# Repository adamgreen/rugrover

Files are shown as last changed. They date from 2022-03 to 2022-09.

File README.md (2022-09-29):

# Rug Rover
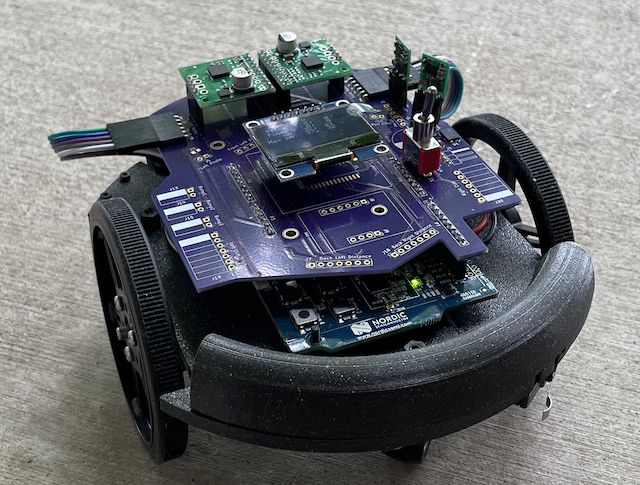
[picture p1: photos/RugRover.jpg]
RugRover Photo of Work In Progress


## **Project on Hold**
I am putting this project on hold for a few months while I switch back to my [Robomagellan robot project](https://github.com/adamgreen/Ferdinand20/#readme) in hopes of the SRS Robothon competition being run in 2023. I will take lessons learned this year while working on my RugRover and apply them to my Robomagellan bot, Ferdinand20.

## Project Overview
My copy of Mobile Robotics

When I first started pursuing robotics as a hobby back in the late 1990s, one of the first books I read was ["Mobile Robots: Inspiration to Implementation" by Joseph L. Jones and Anita M. Flynn](https://www.amazon.com/Mobile-Robots-Inspiration-Implementation-Second/dp/B0087P7X2S). I just read it again recently and the core lessons covered by the book are just as useful today as they were back at that time even though some of the technology discussed is now a bit out of date. The mechanical, electrical, motor physics, and behavior based programming topics covered are all still relevant. The Motorola 68HC11 microcontroller and Interactive C programming language are examples of some of the more dated topics.

After reading the book for the first time, I ordered one of the [Rug Warrior Pro kits](http://www.robotbooks.com/rug_warrior.htm) and assembled it. I enjoyed putting it together but never did a lot of experimentation with it as I never really got one of the wheel encoders to work properly. It seemed to pick up noise from the motor as erroneous encoder tick counts.

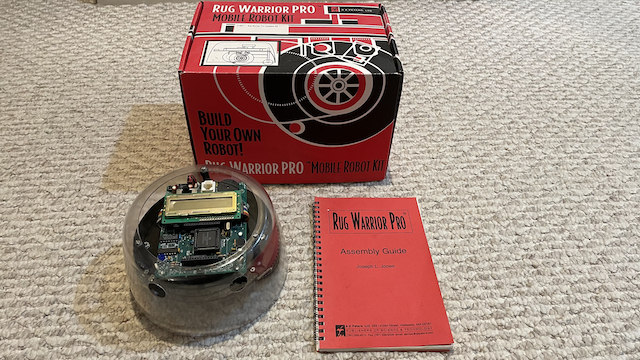
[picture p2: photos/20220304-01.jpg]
My original Rug Warrior Pro


Having recently reread the book, I thought it would be fun to build a comparable robot using more recent technology. This Rug Rover project is my attempt to build such a robot. It features will include:
* Similar sensors/actuators:
  * Motors with encoders
  * IR proximity sensors
  * Bumper switches
  * Microphone
  * Speaker
  * Pyroelectric sensor
  * Photo Cell light level detectors
  * LCD
* Add in IR based downward facing cliff detectors so that I can run the robot in my loft and hopefully write software that stops it from trying to make a run down the stairs.
* More modern nRF52 BLE capable microcontroller:
  * Exploit the BLE capabilities of this microcontroller to enable wireless debugging and programming.
  * Program in C/C++ using GCC.
  * Debug code using GDB.
* Mechanical components will be designed in CAD and 3D printed.
* Use KiCAD to design a custom PCB for this bot. The first iteration of the PCB will be a shield for a nRF52 development kit that I already own. Later I can design a new PCB that uses a small nRF52 module, like those [offered by Adafruit](https://www.adafruit.com/product/4077).

## Reading List
In addition to reading ["Mobile Robots: Inspiration to Implementation" by Joseph L. Jones and Anita M. Flynn](https://www.amazon.com/Mobile-Robots-Inspiration-Implementation-Second/dp/B0087P7X2S) I have also read a few other books to learn more about robot design, building, and programming while working on this project:

<a href="https://www.amazon.com/Navigating-Mobile-Robots-Systems-Techniques/dp/156881058X">Navigating Mobile Robots: Systems and Techniques</a>
<a href="https://www.amazon.com/Kalman-Filter-Beginners-MATLAB-Examples/dp/1463648359">Kalman Filter for Beginners with MATLAB Examples</a>

**Note:** A free PDF version of the **Navigating Mobile Robots book by Borenstein et al** shown above is also available [here](http://www-personal.umich.edu/~johannb/Papers/pos96rep.pdf).

## Bill of Materials
| Quantity | Part Name / Link |
|---|-|
| 2 | [63:1 Metal Gearmotor 20Dx43L mm 6V CB with Extended Motor Shaft](https://www.pololu.com/product/3714) |
| 1 | [Magnetic Encoder Pair Kit for 20D mm Metal Gearmotors, 20 CPR, 2.7-18V](https://www.pololu.com/product/3499) |
| 2 | [TB9051FTG Single Brushed DC Motor Driver Carrier](https://www.pololu.com/product/2997) |
| 1 | [Pololu Multi-Hub Wheel w/Inserts for 3mm and 4mm Shafts - 80×10mm, Black, 2-Pack](https://www.pololu.com/product/3690) |
| 1 | [Supporting Swivel Caster Wheel - 1.3" Diameter](https://www.adafruit.com/product/2942) |
| 1 | [Pololu 3.3V, 500mA Step-Down Voltage Regulator D24V5F3](https://www.pololu.com/product/2842) |
| 1 | [Pololu 5V, 500mA Step-Down Voltage Regulator D24V5F5](https://www.pololu.com/product/2843) |
| 1 | [Pololu 12V Step-Up Voltage Regulator U3V40F12](https://www.pololu.com/product/4016) |
| 1 | [Adafruit I2S 3W Class D Amplifier Breakout - MAX98357A](https://www.adafruit.com/product/3006) |
| 1 | [Mini Oval Speaker - 8 Ohm 1 Watt](https://www.adafruit.com/product/3923) |
| 1 | [Adafruit PDM MEMS Microphone Breakout](https://www.adafruit.com/product/3492) |
| 1 | [Graphical OLED Display: 128x64, 1.3", White, SPI](https://www.pololu.com/product/3760) |
| 1 | [MCP23018T-E/SO - I/O Expander 16 I²C 3.4 MHz 28-SOIC](https://www.digikey.com/en/products/detail/microchip-technology/MCP23018T-E-SO/2002549) |
| 2 | [VL6180X Time-of-Flight Distance Sensor Carrier with Voltage Regulator, 60cm max](https://www.pololu.com/product/2489) |
| 5 | [VL53L1X Time-of-Flight Distance Sensor Carrier with Voltage Regulator, 400cm Max](https://www.pololu.com/product/3415) |
| 2 | [Photo cell (CdS photoresistor)](https://www.adafruit.com/product/161) |
| 3 | [Snap-Action Switch with 15.6mm Bump Lever: 3-Pin, SPDT, 5A](https://www.pololu.com/product/1405) |
| 1 | [PIR Motion Sensor](https://www.pololu.com/product/2731) |
| 1 | [Adafruit Precision NXP 9-DOF Breakout Board - FXOS8700 + FXAS21002](https://www.adafruit.com/product/3463) |
| 1 | [Diode Schottky 60 V 7A Surface Mount TO-277A ](https://www.digikey.com/en/products/detail/vishay-general-semiconductor-diodes-division/SS10P6-M3-86A/2152231) |
| 1 | [Toggle Switch SPDT Through Hole](https://www.digikey.com/en/products/detail/e-switch/100SP1T1B4M2QE/378824?s=N4IgTCBcDaIKIHEwGYCsqC0A5AIiAugL5A) |
| 1 | [Rechargeable NiMH Battery Pack: 6.0 V, 2200 mAh, 3+2 AA Cells, JR Connector](https://www.pololu.com/product/2224) |
| 2 | [Red Dirt Derby 2 oz Tungsten Putty Weights](https://www.amazon.com/Red-Dirt-Derby-Tungsten-Pinewood/dp/B06Y5FDLL6) |
| 1 | [1/4" OD Black Latex Tubing for Bumper Skirt Standoffs](https://www.amazon.com/LATEX-TUBING-602-BLACK-10FT/dp/B074NCLZSW) |
| 1 | [Nordic Semiconductor nRF52 Development Kit](https://www.digikey.com/en/products/detail/nordic-semiconductor-asa/NRF52-DK/5773879) |
| X | Already owned 0805 passives, 0.1" headers, etc. |
| X | Already owned M2, M2.5, and M3 hardware |

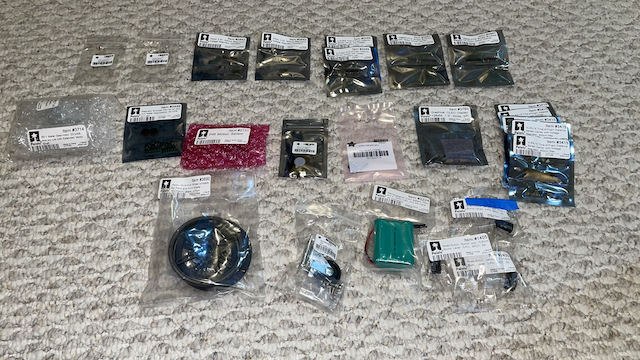
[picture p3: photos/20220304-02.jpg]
Parts


**Notes:** I didn't end up with enough spare pins on version 1 of the PCB to connect the microphone and I2S audio components. I will experiment with these devices off of the robot for now and then add them on the next revision of the board.

## Mechanical Design
When it comes to robot building, the mechanical portions are my weakest area. On some other robot projects I have started with software drivers and then never got around to even starting on the mechanical portions since I wasn't really looking forward to it. Best to get it out of the way first on this project. Doing it first also means that I have something physical to look at and hold earlier in the project to help keep me motivated.

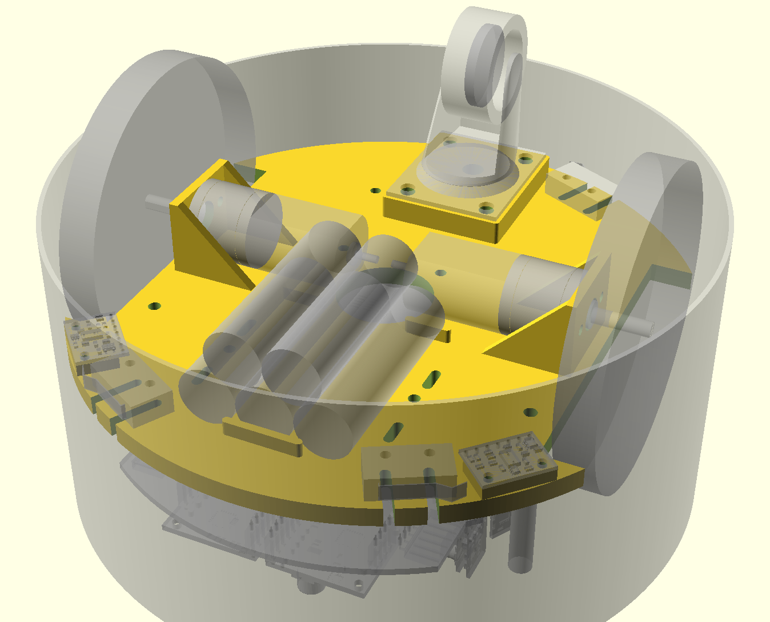
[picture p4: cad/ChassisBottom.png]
Chassis Bottom


**Mechanical Highlights:**
* 3D print the mechanical parts for this robot in PETG.
* Use OpenSCAD for the 3D design.
* The following parts will be mounted to the underside of the robot chassis:
  * 2 x Motors
  * 1 x Caster
  * 2 x Cliff Detection Sensors (VL6180X) mounted in front of the wheels.
  * 3 x Micro Switches to detect bumper collisions.
  * 1 x 5 cell (6V) NiMH rechargeable battery.
* Chassis has holes for attachment of following parts to the topside of the chassis:
  * 5 x Standoffs for Nordic nRF52-DK Development Kit PCB to which shield with remaining sensors/actuators will be mounted.
  * 3 x Flexible Rubber Tube Standoffs to which the bumper skirt is attached, allowing bumper to move and press against micro switches when an obstacle is encountered.
  * A separate curved cylindrical 3D printed holder that goes on the back of the robot to hold ~100g of tungsten counter weight. This moves the center of mass closer to the caster so that the robot doesn't nose dive during quick decelerations. Only having room for the batteries at the front of the bot increased the need for this counterweight.
* A separate bumper skirt is printed to enclose the robot.
  * It is mounted to the chassis on flexible rubber tube standoffs like the Rug Warrior Pro.

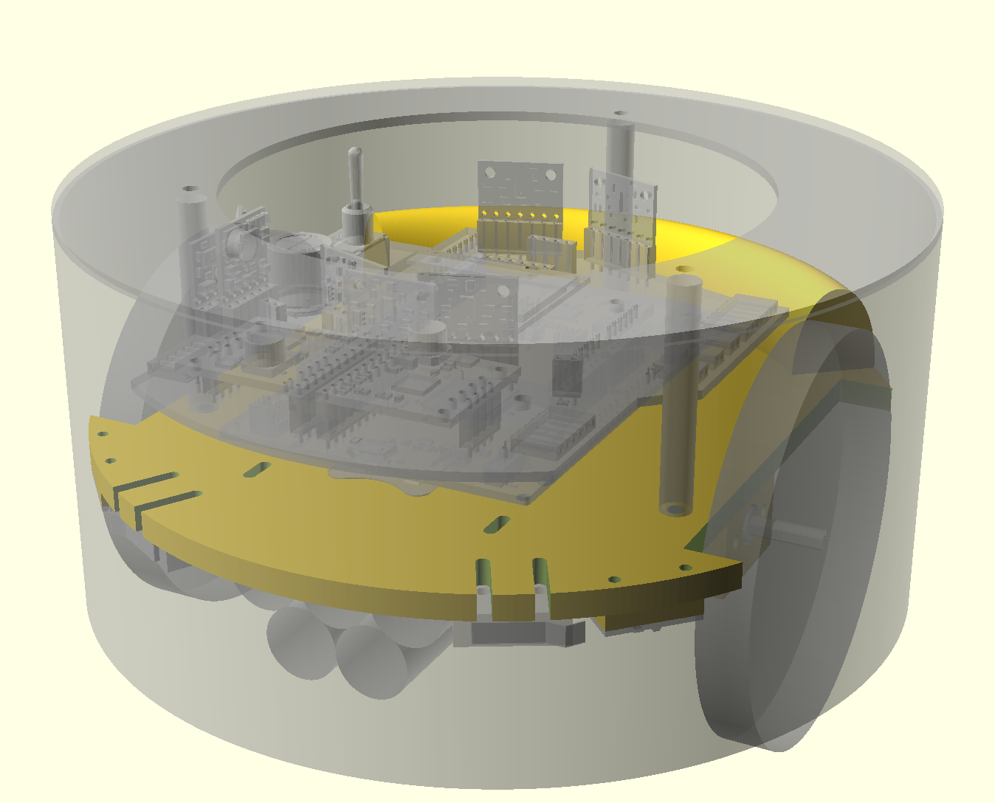
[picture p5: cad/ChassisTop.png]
Chassis Top


**Lessons Learned:**
* The [caster](https://www.adafruit.com/product/2942) I used on this robot is probably too large for the size of the robot. Its size makes it difficult to concentrate the mass over the caster by placing heavy things like the batteries near it on the bottom. I now see why the original RugWarrior Pro used the smaller non-swiveling ball caster. It took up less space and allowed the battery pack to be placed between the axle and the caster.
* [Tungsten putty](https://www.amazon.com/Red-Dirt-Derby-Tungsten-Pinewood/dp/B06Y5FDLL6) is actually a soft moving liquid. The putty I placed in the cylindrical 3D printed holder at the back of the robot leaked out over time and some of it flowed out into the rear micro switch. I was able to take the robot apart and clean up the leaked putty. I designed and printed a bottom for the holder that I welded in place with a soldering iron to contain the tungsten putty inside.

## Electronics Design
Once I had the mechanical design mostly figured out, I moved onto the design of the electronics in [KiCad](https://www.kicad.org).

**Electronic Highlights:**
* The initial version of the electronics will use the [Nordic nRF52 DK](https://www.nordicsemi.com/Products/Development-hardware/nrf52-dk) as its base and the custom robot electronics will be added as a custom shield.
* The shield design is 4-layer to make it easier to route the signals all around the board without worrying about ground and power. The layout is a bit complicated as the Arduino header format used by the nRF52 DK has most of the signals on one side of the board but I want to place input/output connectors on both sides of the board.
* Most of the sensors and actuators are connected to the PCB via 0.1" headers.
* Version 1 of the shield includes:
  * Dual TB9051FTG motor controllers
  * Quadrature motor encoders
  * Dual photo cells
  * PIR motion sensor
  * Three switches for bumper skirt obstacle detection
  * SPI based OLED screen
  * One I2C bus for connection to:
    * 5 x VL53L1X ToF Obstacle Detection Sensors (3 front facing & 2 back facing).
    * 2 x VL6180X ToF Cliff Detection Sensors mounted in front of the wheels.
    * 1 x Adafruit Precision NXP 9-DOF IMU
    * 1 x 16 channel MCP23018 I/O port expander used for:
      * Asserting VL53L1X and VL6180X XSHUT pins to init each one separately and give them unique I2C addresses.
      * Reading of the multiple VL53L1X and VL6180X GPIO pins.
 * Multiple voltage supplies:
   * 6V Directly from Batteries for Motors
   * 5V from Buck Regulator for TB9051FTG Motor Controllers
   * 12V from Boost Regulator for PIR Sensor
   * 3.3V from Buck Regulator for rest of Electronics

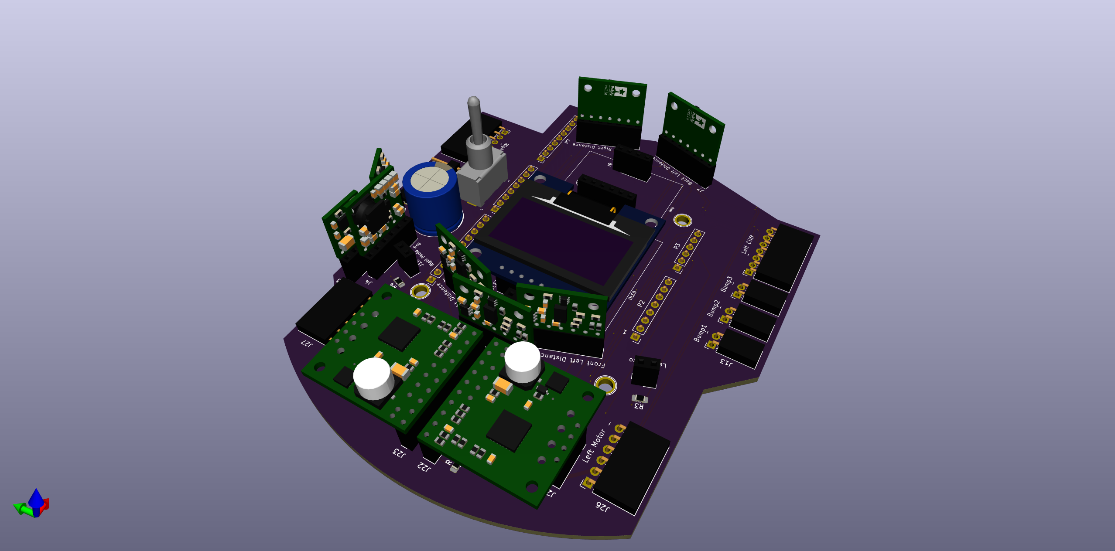
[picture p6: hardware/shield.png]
3D Board View
</br>
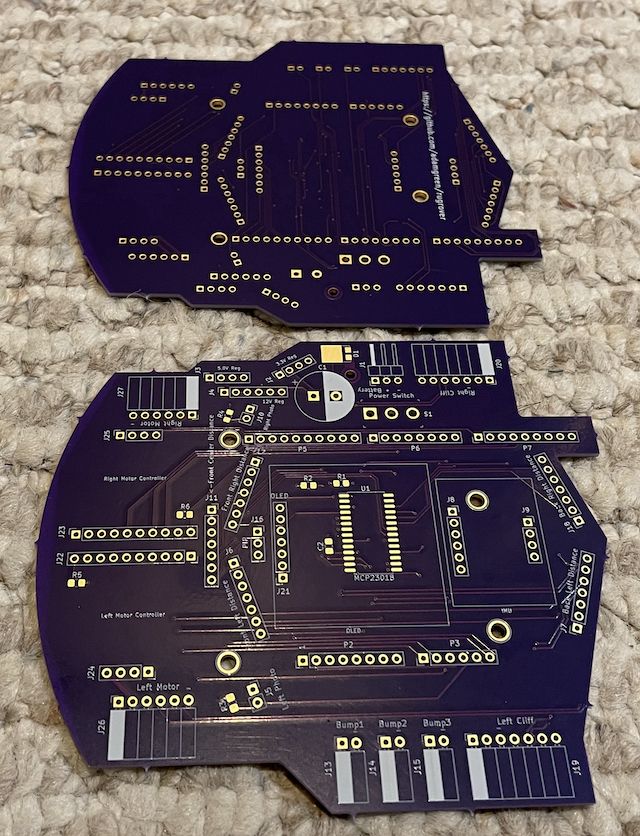
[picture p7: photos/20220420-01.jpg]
Photo of boards back from OSHPark


[Schematic PDF](hardware/shield.pdf)</br>

## Software
Once the mechanical and electronics were far enough along I could start writing the software. This should be where I spend the most amount of time. I will provide links to notes about each software component as I write its code.

**Software Components:**
* [mriblue Debug Monitor](mriblue/README.md#mriblue): A FLASH resident bootloader and debug monitor that runs on the nRF52832 to enable wireless debugging and programming over Bluetooth Low Energy (BLE) from GDB.
* [SH1106 SPI based OLED Driver](software/OLED_SH1106/):
  * An [Adafruit GFX](https://github.com/adafruit/Adafruit-GFX-Library) based display driver.
  * The drawing primitives just modify an in-memory version of the display's frame buffer.
  * A separate refresh() method is used to copy that frame buffer to the SH1106 OLED driver.
  * The refresh() copy makes use of the nRF52's SPI Master peripheral's EasyDMA functionality to perform most of this SPI transfer in the background with little CPU intervention. The CPU is just used to setup the transfer for each of the 8 frame buffer pages.
* [QuadratureDecoderHardware](software/QuadratureDecoder/QuadratureDecoderHardware.h): This driver uses the QDEC peripheral on the nRF52832 to count quadrature encoder ticks. It requires almost no CPU cycles but there is only 1 instance on the microcontroller so I use it for the left encoder only.
* [QuadratureDecoderSoftware](software/QuadratureDecoder/QuadratureDecoderSoftware.h): This driver uses the GPIOTE to fire an ISR on each edge of both the A and B signals from a quadrature encoder. The ISR uses the previous and current encoder signal states to determine if the count should be incremented or decremented. A maximum of 4 encoders can make use of this library if nothing else is making use of the nRF52's 8 GPIOTE channels. The driver needs 2 GPIOTE channels for each encoder, 1 per encoder signal.
* [SAADCScanner](software/SAADCScanner/SAADCScanner.h): This driver runs in the background, reading the specified analog channels (up to 8 on the nRF52832) in a loop using the nRF52's SAADC peripheral:
  * At the end of each loop, an ISR is triggered to process the most current readings. This allows for minimal CPU overhead.
  * It can be configured for manual scanning rather than continuously scanning in the background. I am currently using it this way since it would run at 50kHz in auto mode and the ISR kept showing up in call stacks when I profiled the code.
  * The application can read out a channel's value at a rate slower than the ISR firing rate. The returned structure contains the minimum, maximum, and mean values seen since the last read.
  * The application can also specify trigger limits for the minimum and/or maximum analog values to be expected. Readings outside of these limits will be tracked in the returned structure and can also trigger a callback to a caller provided ISAADCScannerNotification interface.
  * This driver is currently only used to monitor the motor currents for each wheel. In the future it can be used to monitor the light levels detected by the 2 photocells.
* [DualTB9051FTGDrivers](software/DualTB9051FTGDrivers/DualTB9051FTGDrivers.h): This driver allows for the control of 2 Toshiba TB9051FTG H-bridge chips, one for each motor on the robot. It uses 4 channels of the nRF52's PWM peripheral to control the torque and speed of the motors with minimal CPU intervention.
* [GlobalTimer](software/GlobalTimer/GlobalTimer.h): Uses TIMER2 to implement an Arduino like ```micros()``` API to return a 32-bit value indicating the number of microseconds since reset.
* [PID](software/PID/PID.h): Header only class that implements a PID (proportional, integral, derivative) algorithm. It is inspired by [Brett Beauregard's Arduino PID Library](https://github.com/br3ttb/Arduino-PID-Library/) and the [PID e-book available on controlguru](http://www.controlguru.com).
* [DifferentialDrive](software/DifferentialDrive/DifferentialDrive.h): This driver implements closed loop control of RugRover's differential drive. It is built on top of the **DualTB9051FTGDrivers** and Quadrature Decoder libraries. It also has a getStats() method which exposes internal state of the motors, encoders, and PID algorithm to the user:
  * The requested velocity and the actual measured velocity of each wheel.
  * The running total of encoder ticks for each wheel.
  * The motor power (-100% to 100%) being used for each wheel.
  * The most recent motor current measurement (mA) taken for each wheel.
  * The maximum motor current measurement (mA) taken for each wheel so far.
  * Whether any motor faults or over-current events have been detected by the motor drivers.
  * The mAh consumed by the motors since reset.
  * A flag to indicate whether the PID is running in manual or auto mode.
* [Navigate](software/Navigate/README.md#navigate-class): Class used to navigate between a list of user specified waypoints and track the real world location of the robot based on wheel odometry.
* [CircularBuffer](software/CircularBuffer/CircularBuffer.h): Generic lock-free circular buffer that supports multiple producers and consumers.
* [I2CAsync](software/I2CAsync/I2CAsync.h): This driver makes it easier to use the nRF52's TWIM peripheral asynchronously. It makes use of the `CircularBuffer` to allow ISRs running at different interrupt priorities to communicate with several different I2C devices.
* [AdafruitPrecision9DoF](software/AdafruitPrecision9DoF/AdafruitPrecision9DoF.h): This driver uses the `I2CAsync` driver to communicate with the `FXOS8700CQ` accelerometers/magnetometers and the `FXAS21002C` gyros.
  * The desired refresh rate (100Hz, 200Hz, or 400Hz) is specified in the constructor.
  * The `FXOS8700CQ` will pull a pin low when the next sample is ready at the specified rate.
  * This falling edge generates an interrupt that causes the next I2C reads of the accelerometers, magnetometers, and gyros to be queued up in the `I2CAsync` queue.
  * The `getRawSensorValues()` method, typically called from the main thread, will block until all of the queued up reads are completed.
* [OrientationKalmanFilter](software/KalmanFilter/OrientationKalmanFilter.h): Implements a Kalman filter which takes the raw accelerometer, magnetometer, and gyro measurements from the `AdafruitPrecision9DoF` object and generates a 3D orientation quaternion.
  * It also contains a method which can extract the compass heading from this 3D orientation as well.
  * The code for this filter was based on what I learned from reading ["Kalman Filter for Beginners with MATLAB Examples" by Phil Kim](https://www.amazon.com/Kalman-Filter-Beginners-MATLAB-Examples/dp/1463648359). The system model used in this filter came from Chapter 13 of this book.
  * I documented many of the required calibration steps [earlier while working on my Ferdinand14 project](https://github.com/adamgreen/Ferdinand14#august-19-2014).
  * The [processing/calibration folder](processing/calibration/) contains a port of the calibration program which will work with this robot. The robot does need to be running the "Test IMU Raw" option from the debug menu to send the required measurements to this calibration program.
  * The [processing/orientation folder](processing/orientation/) contains a program that visualizes the 3D orientation of the robot in real time. The robot needs to be running the "Test IMU Orientation" option from the debug menu in order to send the required quaternion data over BLE to this program.
  * Both of the processing programs above use a TCP/IP socket to connect to the `mriblue` program on port 3334. This gives it access to extra data sent from the robot over BLE that isn't meant for GDB.
* [HeadingKalmanFilter](software/KalmanFilter/HeadingKalmanFilter.h): Implements a Kalman filter which fuses Z axis gyro angular rate measurements with angle heading change measurements calculated from wheel odometry.
  * The code for this filter was also based on what I learned from reading ["Kalman Filter for Beginners with MATLAB Examples" by Phil Kim](https://www.amazon.com/Kalman-Filter-Beginners-MATLAB-Examples/dp/1463648359).
  * The system model used by this filter was one I created on my own. It tracks:
    * The current heading angle in radians.
    * The current gyro angular turn rate in radians/sec.
    * The estimate of the gyro drift in radians/sec. Having an estimate of this value allows for the filter to obtain a more accurate turn rate from the gyro than possible otherwise.
  * I determined the first two variance values to place in the Q matrix by setting the `DEBUG_CALCULATE_STATS_FOR_SYSTEM_MODEL` macro to true in [main.cpp](software/main.cpp) so that it would dump stats about how much this model tended to deviate from the real world while just using wheel odometry. I then set the variance for the drift parameter to 0.0 since the model maintains it as a constant and in the real world it should vary slowly over time.
  * The `GYRO_ERROR` was calculated and dumped by the orientation.pde utility while I was calibrating the IMU for the OrientationKalmanFilter.
  * I estimate that the `ODOMETRY_ERROR` error is typically the result of a +/- 1 encoder tick's influence on the wheel odometry calculation of the heading angle delta.

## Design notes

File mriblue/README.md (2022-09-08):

# mriblue
What is Yak Shaving?

This was one of the yak shaving projects I got sidetracked with at the beginning of the software development for the RugRover. The name of this yak shaving project is "mriblue". It is an enhanced version of my [MRI debug monitor](https://github.com/adamgreen/mri#readme) which allows for GDB debugging of the nRF52832 Cortex-M4F microcontroller over Bluetooth Low Energy (BLE). This will allow me to sit with my feet up while programming/debugging the RugRover on the floor. No reaching down to connect and disconnect cables.

## mriblue Features
* Supports both wireless programming and debugging from the GNU Debugger, GDB:
  * It supports GDB's "load" command for programming the robot with new code.
  * It supports hardware breakpoints.
  * It supports data watchpoints.
  * It supports single stepping.
  * It supports semihosting, allowing I/O to be completed against files on my Mac.
    * This includes printf() output being sent wirelessly to the GDB console.
* It provides wireless connectivity using the built-in BLE capabilities of the nRF52 microcontroller.
* No extra debug hardware is required. It is a monitor which runs directly on the nRF52 microcontroller being debugged.
* High priority code can't be debugged but if a crash should occur in such code, a crash dump will be generated and placed in FLASH by mriblue instead. Once the dump has been saved away, the device will reset and mriblue will automatically come up in crash dump debugging mode so that GDB can use the dump to query the state of the device at the time of the crash.
* It multiplexes GDB packets and binary application data over the same BLE connection.
* It is open source.

## mriblue Monitor Commands
When using GDB you can send a few special commands to the mriblue debug monitor:
* **"monitor reset"** flags the device for reset. Follow it with a **"continue"** command to actually reboot the microcontroller. This also clears a crash dump out of the FLASH so that you can switch back to a live CPU debugging session.
* **"monitor resetbreak on|off"** enables or disables the automatic halting of the program in its Reset_Handler during bootup. This is persisted across power cycles in FLASH.
* **"monitor showfault"** will display extra information to the GDB console about the nature of a fault (using the Cortex-M fault status registers).
```console
(gdb) monitor showfault

**Hard Fault**
  Status Register: 0x40000000
    Forced
**Bus Fault**
  Status Register: 0x82
    Fault Address: 0xffffffff
    Precise Data Access
```

## mriblue vs OpenOCD
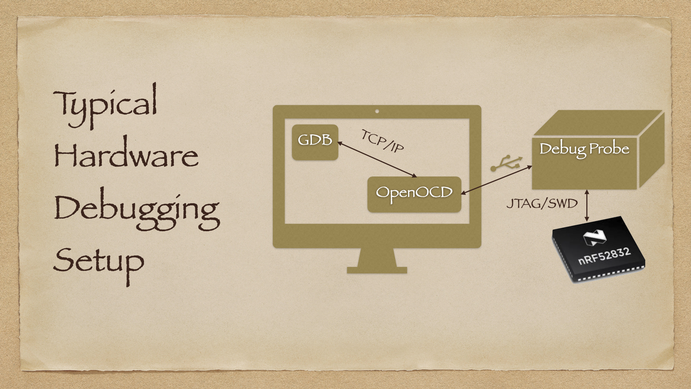
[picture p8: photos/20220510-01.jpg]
Typical GDB Debugger Setup
</br>
If you have ever done any GDB debugging of a microcontroller in the past then you have probably used a setup like that shown above:
* You run a remote stub like OpenOCD on the same computer as you run GDB.
* GDB uses TCP/IP to communicate with OpenOCD.
* It is OpenOCD which understands GDB's remote debug protocol and translates it into the necessary debug probe commands.
* OpenOCD communicates with the debug probe using an external interface such as USB.
* The debug probe will then use JTAG or SWD to communicate with the debug access port of the microcontroller.

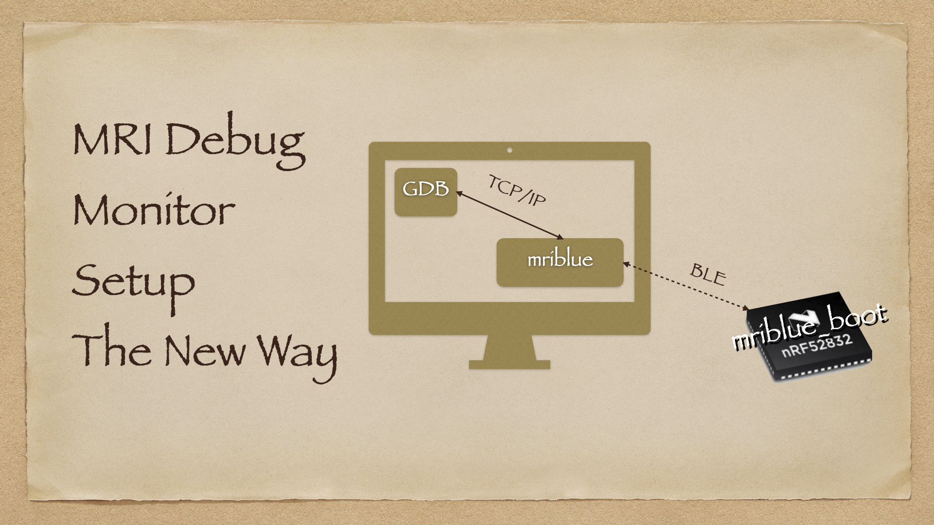
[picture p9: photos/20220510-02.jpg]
mriblue GDB Debugger Setup
</br>
The setup for my mriblue project, shown above, shares some similarities with the OpenOCD setup but also differs in a few key areas:
* It too has a program (only available for macOS) which runs on the same computer as GDB:
  * It is called [mriblue](../mriblue/).
  * GDB also communicates with it over TCP/IP, on port 3333 by default.
  * ~~Unlike OpenOCD, it doesn't have any knowledge of the GDB remote debug protocol. It is just a bridge between TCP/IP and BLE. It could be used to bridge serial traffic from BLE to TCP/IP for any application except that it is explicitly written to find and connect to devices running the mriblue_boot bootloader.~~ It only knows enough about the GDB packet format to send such packets to GDB's socket, on port 3333. It sends any binary data found outside of these GDB packets to another socket, on port 3334 by default. Applications can then be written for the Mac to connect to this socket to visualize and/or log the data. The format of this data is more compact than that found within GDB packets (usually 50% smaller).
* Unlike a typical OpenOCD setup, mriblue requires no special debug hardware. The code which implements the GDB remote debug protocol and talks with the debug access port on the Cortex-M4F core is all contained in the [mriblue_boot bootloader](../mriblue_boot/) which runs directly on the nRF52832 microcontroller alongside the robot's firmware. The next couple of sections will give an overview of how it accomplishes this by sharing FLASH memory and CPU cycles via the NVIC's prioritized interrupts.

## mriblue_boot FLASH Memory Layout
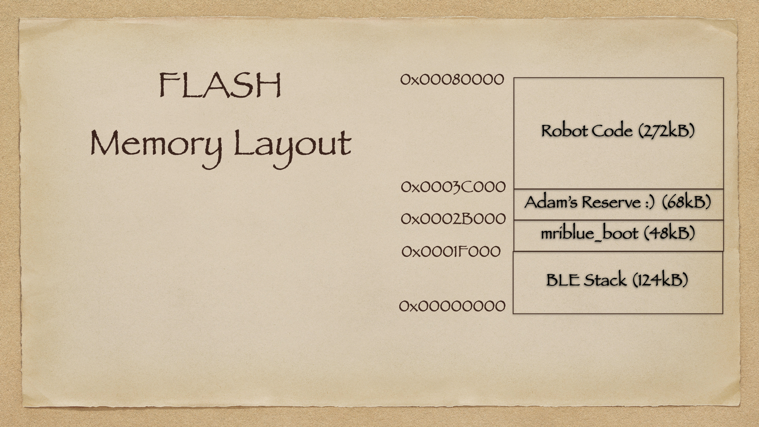
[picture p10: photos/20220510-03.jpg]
FLASH Memory Layout
</br>
The mriblue_boot bootloader resides in FLASH alongside the BLE Stack (Nordic SoftDevice version 132) and the robot code:
* The SoftDevice resides at the beginning of FLASH, at address 0x0000000, like usual.
* Normally the Robot code would come right after the SoftDevice to start at address 0x0001F000. This is where the mriblue_boot now resides so that the SoftDevice will forward exceptions and interrupts to it automatically without any extra configuration.
* The 68kB of FLASH following the bootloader area is reserved for storing of a crash encountered in high priority code. It is large enough to store:
  * 64kB copy of the entire SRAM at the time of the crash. This makes the stack, globals, and heap all available to the debugger when investigating the crash dump.
  * Another 4kB page of FLASH to store the context (CPU registers, MRI debug monitor state, etc) from the time of the crash.
* The robot's main code can then start at 0x0003C000. Now that the robot code and mriblue code live in their own separate areas of memory, it is possible for mriblue_boot to erase the robot code and it itself still function correcly. This means it can be used to load new code into the device as erasing pages is the first step requested when GDB handles a "load" command.

The [interrupt vector table](https://github.com/adamgreen/rugrover/blob/master/mriblue_boot/gcc_startup_nrf52.S#L422) found in the mriblue_boot bootloader is written so that by default every entry in the table will just jump to the corresponding entry in the robot code's interrupt vector table. These defaults are weak implementations so any exception or interrupts that are of interest to mriblue_boot itself will be implemented as strong functions which will override and replace these forwarding entries.

## mriblue_boot NVIC Interrupt Priorities
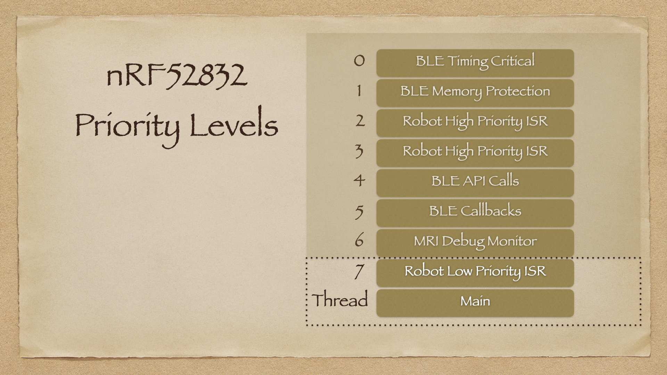
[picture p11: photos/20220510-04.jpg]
Interrupt Priorities
</br>
The previous section showed how mriblue_boot could co-exist with the BLE SoftDevice and robot code in FLASH. Now let's look at how it can share the CPU cycles itself with the robot code and BLE stack. It uses the 8 interrupt priority levels on the nRF52 to make it possible for all these things to run on the same CPU. When MRI has halted the robot code for debugging, it can’t stop everything. It needs to keep the BLE stack running so that it can be used to keep communications open between GDB and itself:
* On Cortex-M microcontrollers, the lower the priority level number, the higher the actual priority.
* In the above diagram, you can see the priority levels that are used by the different components of the system. The more darkly shaded levels (levels 0 to 6) can't be debugged directly by mriblue as they are too high priority. The non-shaded levels (level 7 and Thread/Main) can be halted for the purpose of debugging.
* The BLE stack uses the 2 highest priority levels: level 0 and level 1. It also uses levels 4 and 5.
* mriblue_boot runs at priority level 6 so any time the BLE stack needs to do something to keep up its communication with GDB, it is free to interrupt mriblue_boot and do its work.
* Our robot code can run code at interrupt levels 2, 3, and 7.
  * Levels 2 and 3 are too high priority for MRI to debug. If the robot code running at these 2 levels should cause a fault, a crash dump will instead be written to the reserved area of the FLASH, the microcontroller reset, and then mriblue_blue starts up in a special mode which allows GDB to debug the crash dump rather than the live CPU state.
  * Level 7 ISRs in the robot code can be debugged since they will be halted automatically by the NVIC when the mriblue_boot debug monitor is entered at priority level 6.
  * It can also debug all of the non-interrupt robot code. This is anything you run from your main() function.

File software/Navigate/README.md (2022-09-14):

# Navigate Class
This class serves 2 purposes:
* Track the robot's real world location (in mm) and heading (in radians).
* Automatically navigate between a list of user specified waypoints.

The robot can also accept commands that tell it what speed and direction to go instead of automatically navigating to waypoints. This class will still track the robot's real world location when run in this non-automated fashion.

The origin of the robot's world view is its location at the time of reset. It also views the direction it was facing at the time of reset as 0 degrees with clockwise rotations resulting in positive angles and counterclockwise rotations resulting in negatives angles.

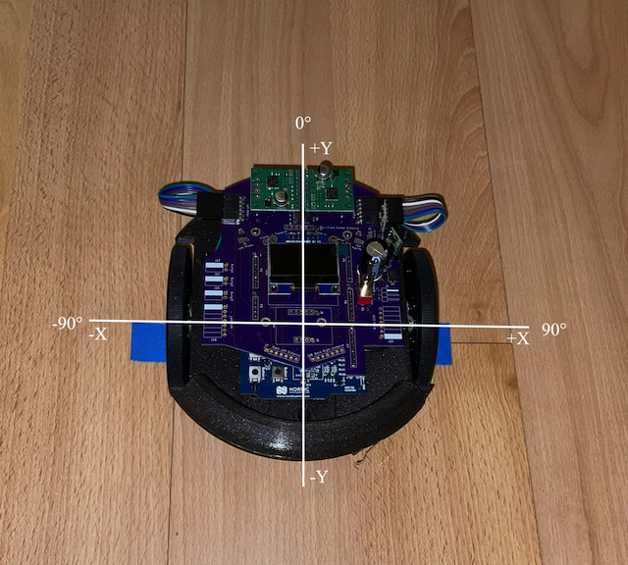
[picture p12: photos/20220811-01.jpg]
Photo of RugRover showing axis


## Constructor
```c++
Navigate(DifferentialDrive* pDrive, float ticksPerRotation,
            float leftWheelDiameter_mm, float rightWheelDiameter_mm, float wheelbase_mm,
            float distanceThreshold_mm, float angleThreshold_radians, float headingRatio, uint32_t brakeSamples,
            float headingPidKc, float headingPidTi, float headingPidTd,
            float distancePidKc, float distancePidTi, float distancePidTd);
```
* **pDrive**: A pointer to the DifferentialDrive object that has been setup for closed loop PID control of the 2 motors on the robot. I thought about deriving the Navigate class from DifferentialDrive or encapsulating it but decided to instead let the caller initialize and own it instead. The parameter list for the ```Navigate::Navigate()``` constructor is already so long, adding the ones needed to initialize DifferentialDrive as well would make it humongous.
* **ticksPerRotation**: The number of encoder ticks that will be generated for each rotation of the wheel. For the motor/encoder combo that I am currently using on the RugRover this will be: **20 ticks/motor_rev * 62.5 gear_ratio = 1250 ticks/wheel_rev**.
* **leftWheelDiameter_mm**: The diameter of the left wheel in mm. Nominally both wheels are supposed to be 80mm in diameter. I will discuss a bit more about how I fine tuned the measurement for both wheels later in the [calibration section](#calibration).
* **rightWheelDiameter_mm**: The diameter of the right wheel in mm. Nominally both wheels are supposed to be 80mm in diameter. I will discuss a bit more about how I fine tuned the measurement for both wheels later in the [calibration section](#calibration).
* **wheelbase_mm**: The distance between the 2 wheels. The CAD design has the distance between the two wheels as 128.1868mm. When I did the calibration process described [below](#calibration) it turned out that this CAD measurement was pretty accurate.
* **distanceThreshold_mm**: How close, in mm, does the robot need to be to a waypoint before it is considered reached.
* **angleThreshold_radians**: How close, in radians, does the robot need to be pointed towards the desired location (next waypoint, etc) before a turn is considered done.
* **headingRatio**: The maximum turning speed while driving forward is constrained so that it doesn't exceed the current drive speed and attempt to run one of the motors in reverse. This ratio specifies how much of the current forward speed should be used for constraining the heading control loop. It should be a positive float value > 0.0f and <= 1.0f.
* **brakeSamples**: When braking between stages, wait for this many samples to return 0 encoder ticks before considering the stop to be complete.
* **headingPidKc, headingPidTi, headingPidTd**: These are the PID (Proportional, Integral, Derivative) parameters for the closed loop control system used for maintaining the desired heading. Currently I just use the P & I terms, leaving the D term set to 0.0f. The [calibration section](#calibration) contains notes on how I calculated them for this robot.
* **distancePidKc, distancePidTi, distancePidTd**: These are the PID (Proportional, Integral, Derivative) parameters for the closed loop control system used for determining the forward travel speed based on distance to the next waypoint. Currently I just use the P & I terms, leaving the D term set to 0.0f. The [calibration section](#calibration) contains notes on how I calculated them for this robot.

## Waypoints
The user can call setWaypoints() to provide a list of ```Position``` structures representing the locations to which the robot should navigate and in which direction the robot should face after it reaches each waypoint. Currently it only makes sense to use the heading field for the last waypoint as the robot will always followup this heading with one that faces the next waypoint. I do have some ideas of how to make beter use of it in the future though.

```c++
struct Position
{
    // Coordinates of this waypoint in mm.
    float x;
    float y;
    // The angle the robot should be turned to face once waypoint is reached. Can be NAN if no turn is desired.
    float heading;
};
```

The robot goes through 2-3 stages for each waypoint:
1. First it turns in place to face the waypoint.
2. Next it drives towards the specified x/y coordinates of the waypoint.
3. It will then turn in place again to face the desired heading if such a heading is given in the waypoints ```heading``` field of its ```Position``` structure.

## update() Method
The method should be called at the PID frequency (currently 100Hz) to update all of the PID based control loops, update the robot's position estimate based on recent wheel movement, and continue to progress through the waypoints.

## drive() Method
This method like the ```update()``` method should be called at the PID frequency but it ignores the waypoint list and instead commands the wheels to spin at the caller specified velocities (in meters/s). It also updates the robot's position estimated based on recent wheel movement.

## Logging
Sometimes I see the robot do something unexpected as it is running along on the floor and I want to take a peek at things like the robot's position and/or heading that would account for why it suddenly decided to do something that I wasn't expecting. I have added 2 methods to allow for logging from within the Navigate class:

```c++
void setLogBuffer(void* pLog, size_t logSize);
bool dumpLog(const char* pFilename);
```

The ```setLogBuffer()``` method allows the user to provide a byte array into which the Navigate module can log. This buffer is provided by the caller so that it responsible for allocating it if it wants to actually make use of it. This way the Navigate module doesn't need to allocate a log buffer that the caller isn't going to make use of or have a way to dynamically allocate it on an embedded platform that isn't well setup for such allocations. This buffer needs to be an even multiple of 4-bytes as that is the size of each sample (only needs to log 8-bit signed values for encoder tick deltas and motor power settings for each of the wheels). This will be used as a circular buffer and will only contain the most recent entries if the test should run longer than there is buffer to hold all of the samples taken during a run.

The ```dumpLog()``` method opens up a .CSV file on the host computer where GDB is running. Compressed 8-bit signed values are logged to memory for each sample so this method will expand these logged values to determine total encoder ticks accumulated, absolute robot's location in mm, and the robot's heading at each sample. This does mean that the samples will be serialized out to the .CSV file in reverse chronological order since this makes the decompression easier.

## Calibration
Odometry requires accurate values for the left/right wheel diameters and wheelbase between the two wheels. The [Navigating Mobile Robots book by Borenstein et al](http://www-personal.umich.edu/~johannb/Papers/pos96rep.pdf) contains a method for calibrating these parameters but I chose to use a simpler approach but still use their clockwise and counterclockwise tests to verify the odometry after calibration.

The debug menu in [software/main.cpp](../main.cpp) has routines which help run tests to calibrate these parameters:
```console
Debug Menu
1. Test Navigate
2. Test PID
3. Run Speed PID calibration
4. Run Heading PID calibration
5. Run Distance PID calibration

Select:
```

### Wheel Diameters
This is the rough process that I used to calibrate the diameter of the wheels:
* Marked location on floor where each wheel starts the test.
* Ran the straight driving test as seen in the console log below:
```console
Debug Menu
1. Test Navigate
2. Test PID
3. Run Speed PID calibration
4. Run Heading PID calibration
5. Run Distance PID calibration

Select: 1

Update odometry settings.
Just press <Return> to keep current setting.
Left Wheel Diameter in mm (80.680000):
Right Wheel Diameter / Left Wheel Diameter ratio (0.996000):
Wheel base in mm (128.186798):

Drive (s)traight, (t)urn in place, (c)lockwise, (x)counter-clockwise: s
```
* Noted the total left/right encoder ticks from the OLED or first line of the test_navigate.csv log file.
* Used a measuring tape to determine the distance each wheel had traveled during the test.

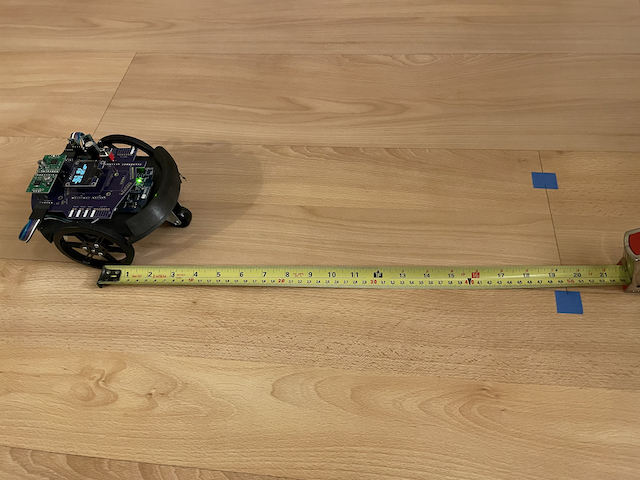
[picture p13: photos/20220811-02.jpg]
Left wheel measurement

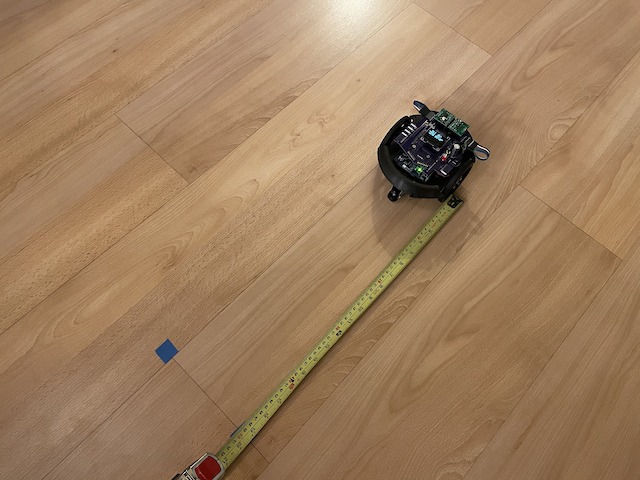
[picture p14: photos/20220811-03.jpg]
Right wheel measurement

* The distance measurements and encoder tick counts were then entered in my [docs/wheel_diameter.numbers spreadsheet](../../docs/wheel_diameter.numbers) to determine better estimates for the actual wheel diameters.

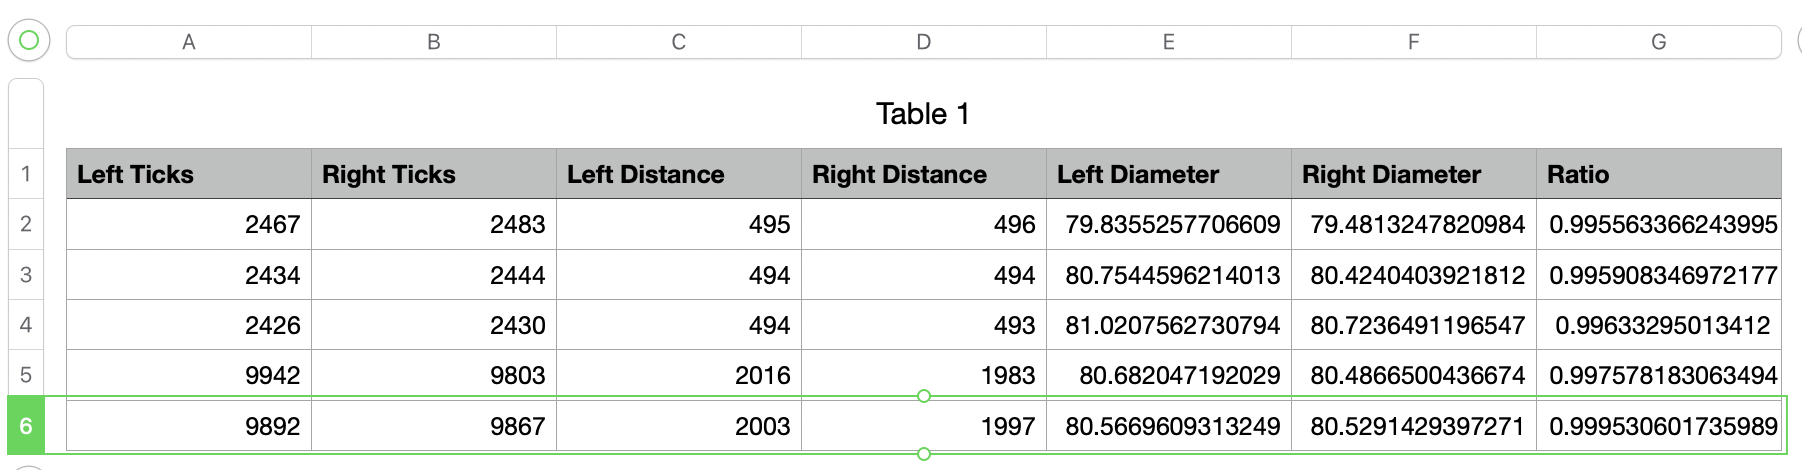
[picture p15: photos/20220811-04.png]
Spreadsheet


### Wheelbase
This is the rough process that I used to calibrate the wheelbase, the distance between the wheels of the robot:
* I drew vertical and horizontal lines going through the center of a piece of paper. I then taped this paper down to the floor and placed the center of the robot over the center of the paper with the horizontal line directly beneath the wheel axles.
* Ran the turn in place test as seen in the console log below:
```console
Debug Menu
1. Test Navigate
2. Test PID
3. Run Speed PID calibration
4. Run Heading PID calibration
5. Run Distance PID calibration

Select: 1

Update odometry settings.
Just press <Return> to keep current setting.
Left Wheel Diameter in mm (80.680000):
Right Wheel Diameter / Left Wheel Diameter ratio (0.996000):
Wheel base in mm (128.186798):

Drive (s)traight, (t)urn in place, (c)lockwise, (x)counter-clockwise: t
```
* Noted the robot's final heading estimate from the OLED or first line of the test_navigate.csv log file.
* Used a protractor to measure the robot wheel's actual angle and compared it to the robot's estimate. I got lucky and the two values just matched but if the robot's estimate was too large then the wheelbase should be increased a bit and vice versa.

### Heading/Distance PI
The Debug Menu on the robot has options for running heading and distance PI calibration routines. These routines oscillate the robot via in place rotations or straight back and forth motions. These test routines are 4 and 5 in the list below:
```console
Debug Menu
1. Test Navigate
2. Test PID
3. Run Speed PID calibration
4. Run Heading PID calibration
5. Run Distance PID calibration
```
Once these tests are done running, they look through the data looking for the range and timings of the oscillations and use them to calculate parameters to model its behavior and can be used to calculate good PI parameters for each of the control loops.

**Example Output from "Run Heading PID calibration"**
```console
Calculated PID Model Parameters
slope1 = 2.914975
slope2 = -3.094060
CO1 = 0.250000
CO2 = -0.250000
Kp* = 12.018072
Өp = 0.114456
Tc = 0.343369
Kc = 0.318056
Ti = 0.801193
```

**Example Output from "Run Distance PID calibration"**
```console
Calculated PID Model Parameters
slope1 = 222.512833
slope2 = -224.032501
CO1 = 0.250000
CO2 = -0.250000
Kp* = 893.090698
Өp = 0.118901
Tc = 0.356702
Kc = 0.004120
Ti = 0.832304
```

These tests also generate .CSV files which can be loaded into a spreadsheet and graphed to see how the process responds to changes in control output.

## Future Improvements
This is a pretty good start to this class but I will probably come back in the future to address a few issues:
* ~~Improve how well it tracks between waypoints. It sometimes takes an unexpected curvy approach.~~
* Have a way to pause at each waypoint and let the caller know when each has been reached so that it can run specific actions at waypoints. And example would be finding and touching a traffic cone when a waypoint close to the cone has been reached.

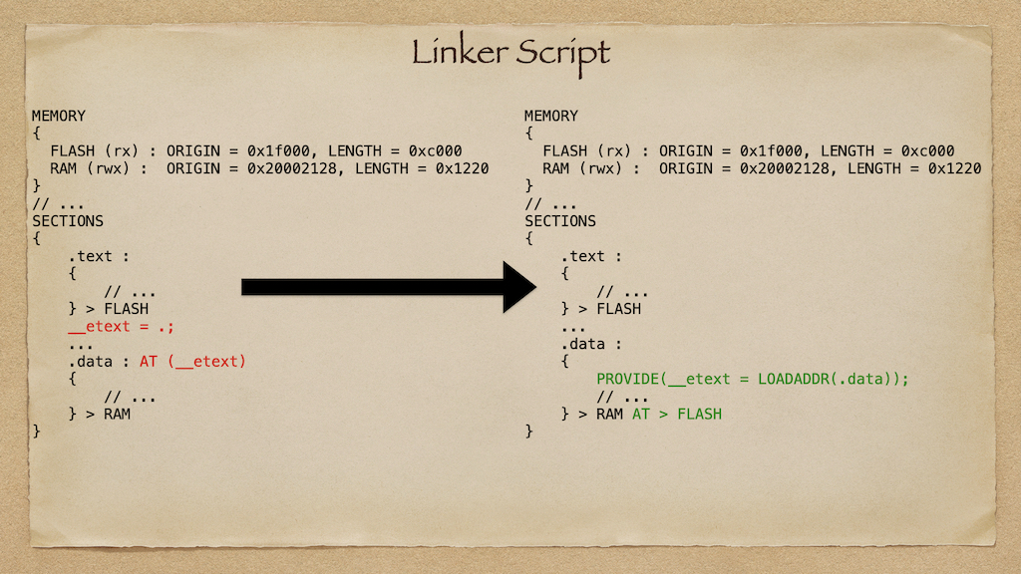
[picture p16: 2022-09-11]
photos/20220911-mriblue.jpg

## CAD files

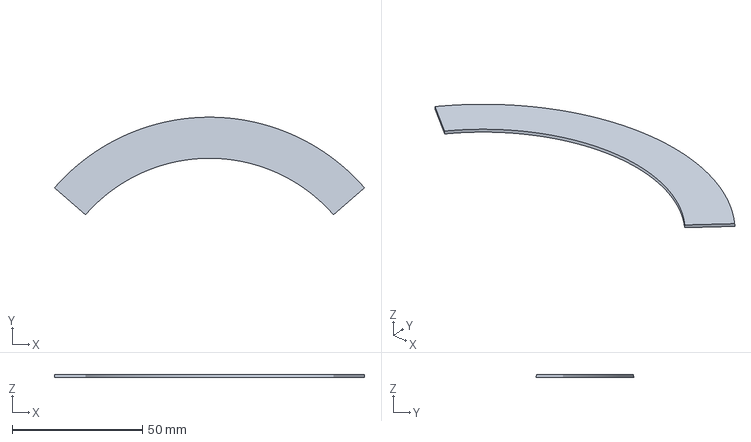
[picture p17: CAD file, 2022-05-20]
cad/WeightHolderBottom.3mf
119.1 x 37.5 x 1.00 mm

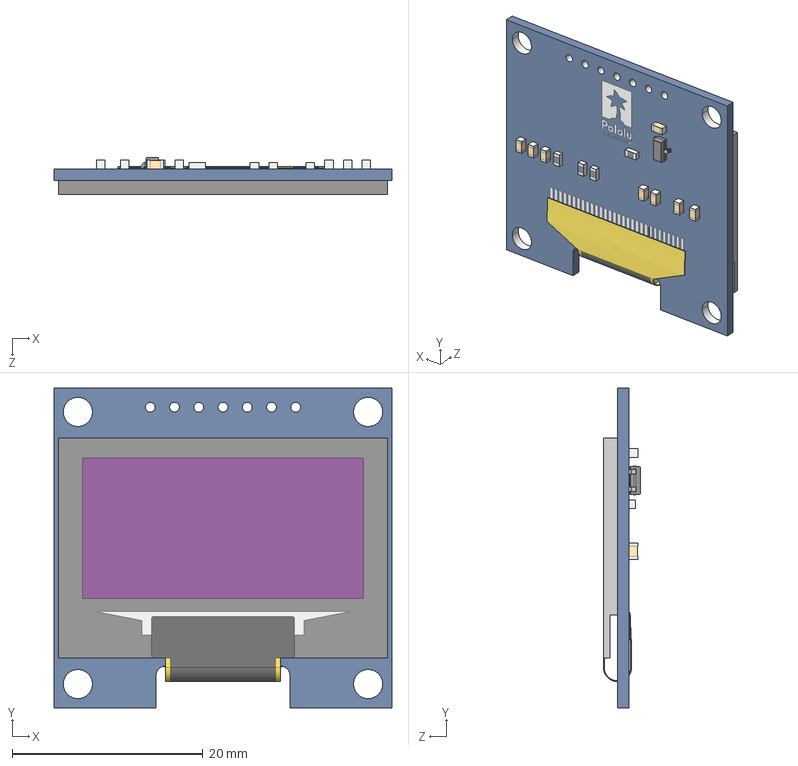
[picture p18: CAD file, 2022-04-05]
hardware/graphical-oled-display-128x64-1.3-white-spi.step
35.4 x 33.5 x 3.90 mm

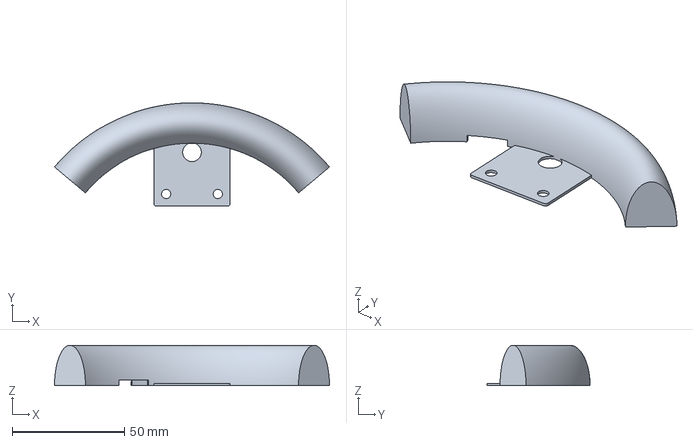
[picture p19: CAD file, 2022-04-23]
cad/WeightHolder.3mf
122.6 x 46.0 x 18.0 mm

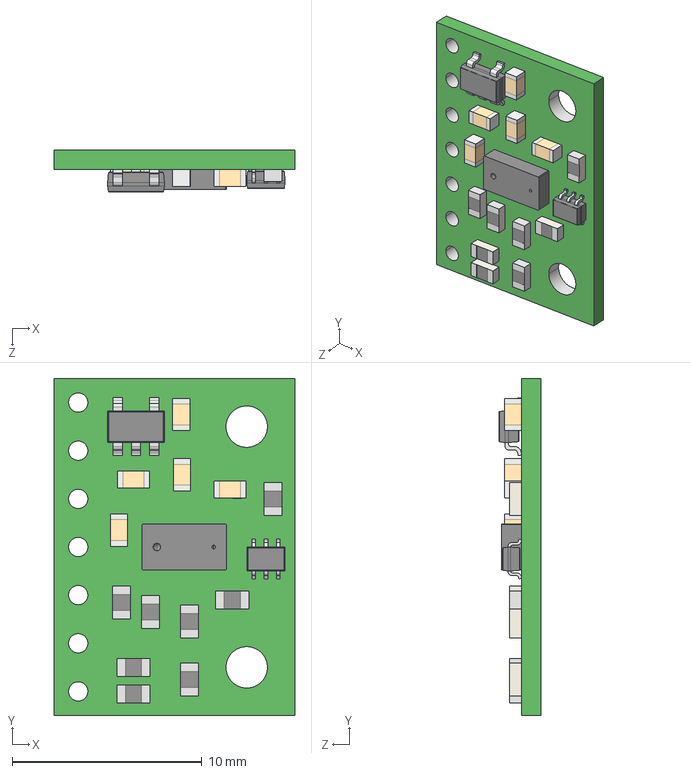
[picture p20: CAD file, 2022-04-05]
hardware/vl53l0x-vl53l1x-vl53l3cx-carrier-model.step
12.7 x 17.8 x 2.21 mm

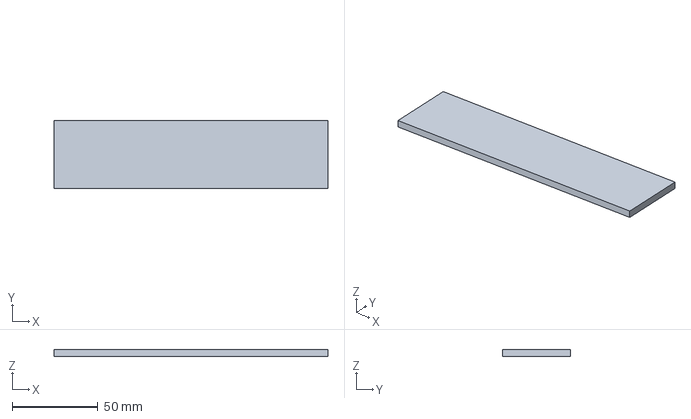
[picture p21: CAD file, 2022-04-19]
cad/FlexTest.3mf
160.0 x 40.0 x 4.00 mm

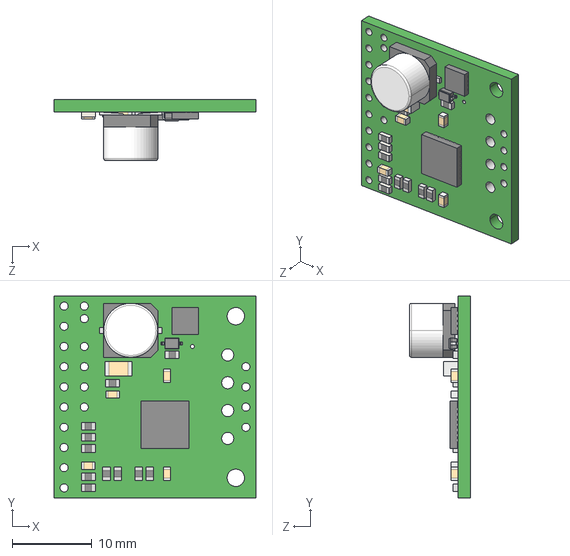
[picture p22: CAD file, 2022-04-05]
hardware/tb9051ftg_single_brushed_dc_motor_driver_carrier.step
25.4 x 25.4 x 7.67 mm

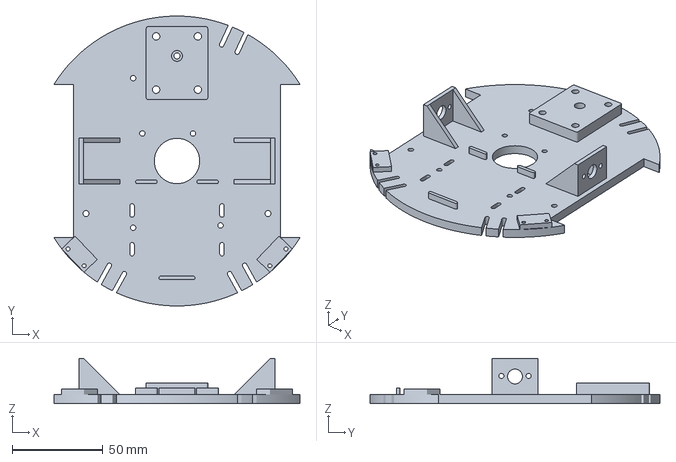
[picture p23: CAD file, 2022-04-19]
cad/Chassis.3mf
135.8 x 160.0 x 25.0 mm

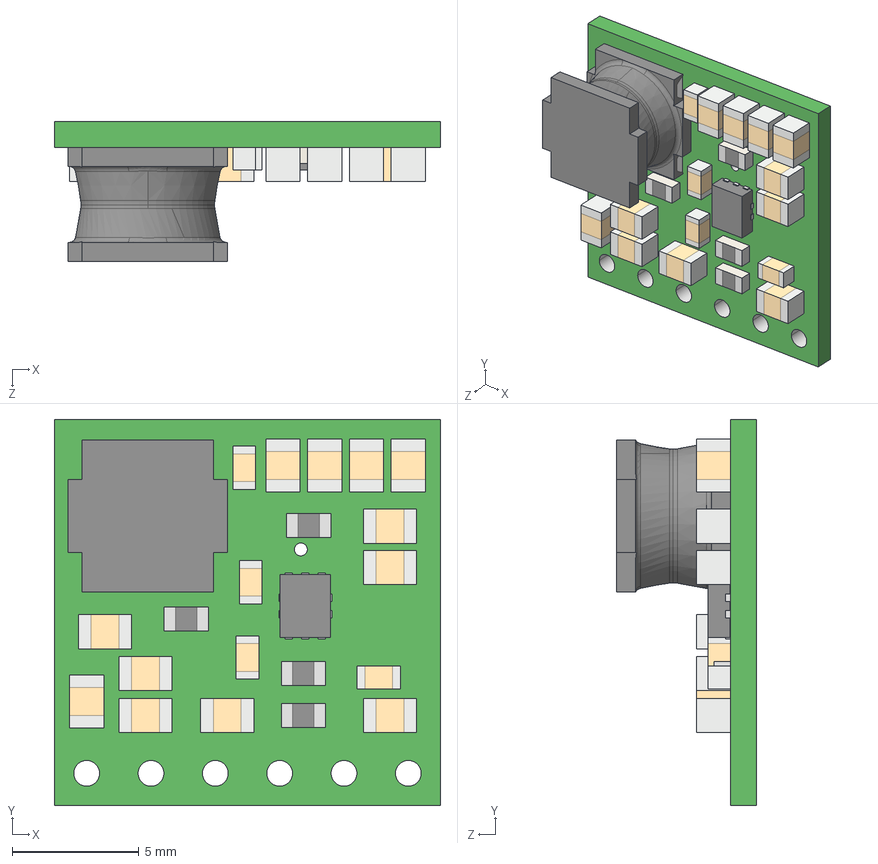
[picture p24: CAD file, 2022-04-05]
hardware/step-up-voltage-regulator-u3v40fx.step
15.2 x 15.2 x 5.51 mm

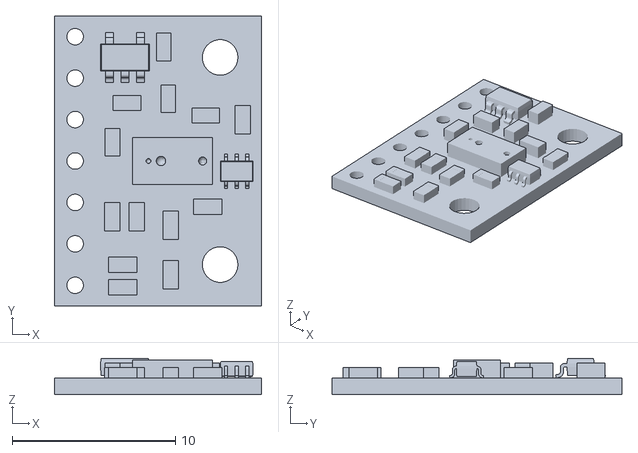
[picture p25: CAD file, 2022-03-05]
cad/vl6180x-carrier.stl
12.7 x 17.8 x 2.21

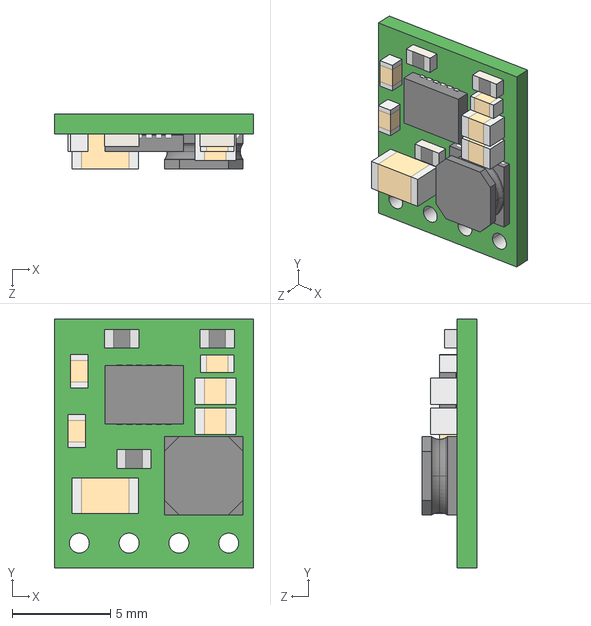
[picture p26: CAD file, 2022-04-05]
hardware/d24v5fx-step-down-voltage-regulator.step
10.2 x 12.7 x 2.82 mm

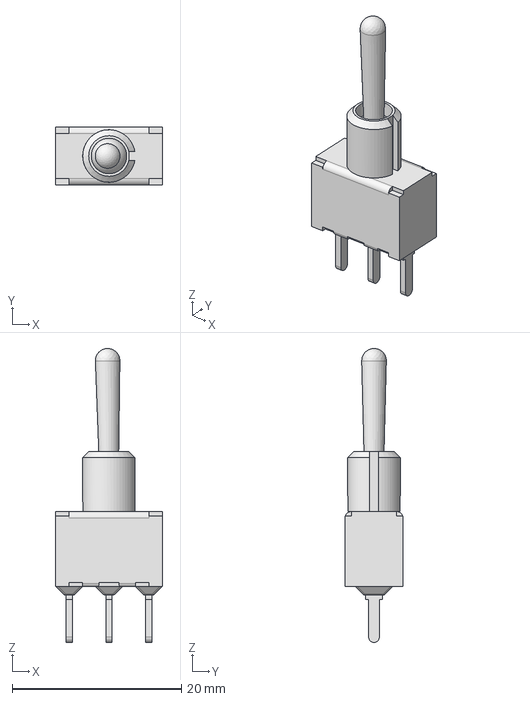
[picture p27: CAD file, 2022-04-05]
hardware/100SPxT1B4M2xE.stp
12.7 x 6.86 x 34.8 mm

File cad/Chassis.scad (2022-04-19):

/*  Copyright (C) 2022  Adam Green (https://github.com/adamgreen)

    This program is free software; you can redistribute it and/or
    modify it under the terms of the GNU General Public License
    as published by the Free Software Foundation; either version 2
    of the License, or (at your option) any later version.

    This program is distributed in the hope that it will be useful,
    but WITHOUT ANY WARRANTY; without even the implied warranty of
    MERCHANTABILITY or FITNESS FOR A PARTICULAR PURPOSE.  See the
    GNU General Public License for more details.
*/
// The chassis for my RugRover bot.

// ************
//  Parameters
// ************
// Motor part dimensions.
//  Gearbox built in 3 pieces where piece separation is represented by 2 rings in this  model.
//  Also has 2 tapped holes for mounting. It also includes the output D-shaft and the collar
//  where the output shaft enters the gearbox.
motorGearboxDiameter = 20.0;
motorGearboxLength = 17.3;
motorGearboxRingOffset = 3.0;
motorGearboxRingWidth = 0.1;
motorGearboxRingDepth = 0.1;
motorGearboxHoleOuter = 17.08;
motorGearboxHoleInner = 12.86;
motorGearboxHoleDiameter = 2.5;     //(motorGearboxHoleOuter - motorGearboxHoleInner)/2;
motorGearboxHoleOffsetRadius = 7.5; //(motorGearboxHoleOuter + motorGearboxHoleInner)/2/2;
motorGearboxHoleDepth = 2.0;
motorGearboxCollarDiameter = 7.0;
motorGearboxCollarDepth = 3.0;
motorGearboxShaftDiameter = 4.0;
motorGearboxShaftIndentDiameter = 3.5;
motorGearboxShaftLength = 14.5;
//  The electric motor attached to the back of the gearbox. Includes shaft sticking out the back
//  along with the electrical connections.
motorDiameter = motorGearboxDiameter;
motorFlatWidth = 15.4;
motorLength = 25.0;
motorCollarDiameter = 6.05;
motorCollarDepth = 1.9-0.7;
motorShaftDiameter = 2.0;
motorShaftLength = 6.0;

// Wheel dimensions.
wheelDiameter = 80.65;
wheelThickness = 10.0;

// Caster dimensions.
//  The wheel itself.
casterDiameter = 29.85;
casterInnerDiameter = 22.40;
casterThickness = 13.2;
casterInnerThickness = casterThickness - 2 * 5.25;
//  The plate which has the thrust bearing and attaches to the bot body.
casterPlateWidth = 38.2;
casterPlateHeight = 31.95;
casterPlateThickness = 1.3;
//  Placement of 4 holes used to mount plate to bot body.
casterHoleDiameter = 4.1;
casterHoleXSpacing = (33.65 + 25.2) / 2;
casterHoleYSpacing = (18.88 + 27.15) / 2;
//  Thrust bearing between plate and arm that holds the wheel.
casterBearingTopDiameter = 28.42;
casterBearingBottomDiameter = 23.0;
casterBearingHeight = 4.1 - casterPlateThickness;
//  Arm that holds the wheel.
casterArmTopDiameter = 25.55;
casterArmBottomRadius = 10.0 / 2;
casterArmBottomWidth = 18.0;
casterArmTopZOffset = 1.0;
casterArmXOffset = 10.0;
casterArmZOffset = 25.0;
casterArmCutoutTopThickness = 1.2;
casterArmCutoutTopWidth1 = 17.4;
casterArmCutoutTopWidth2 = 22.0;
casterArmCutoutBottomWidth = 15.0;

// Dimensions of the VL6180X based cliff detector.
cliffDetectorWidth = 12.7;
cliffDetectorHeight = 17.8;
cliffDetectorMountingHoleDiameter = 2.2;
cliffDetectorMountingHoleXOffset = cliffDetectorWidth - 2.5;
cliffDetectorMountingHoleYOffset = cliffDetectorHeight/2 - 2.5;

// Rough dimensions of bumper switches.
bumperSwitchWidth = 19.8;
bumperSwitchHeight = 10.6;
bumperSwitchThickness = 6.2;
bumperSwitchHoleDiameter = 2.5;
bumperSwitchHoleXOffset = 9.5/2;
bumperSwitchHoleYOffset = -bumperSwitchHeight/2 + 2.9;

// Dimensions of the Nordic nRF52DK PCB.
nRF52DK_Length = 101.6;
nRF52DK_Width = 63.5;
nRF52DK_Thickness = 1.6;
// Location of the mounting holes in the nRF52DK PCB.
nRF52DK_MountingHoles=[[15.24, 50.8+5, 0], [13.97, 2.54+5, 0], [66, 7.62+5, 0], [66, 35.56+5, 0], [96.52, 2.54+5, 0]];

// Dimensions of the AA cells in the Pololu battery packs.
batteryDiameter = 14.6;
batteryLength = 50.4;

// Dimensions of my RugRover shield that to be placed on top of the nRF52 DK.
// How much further above the nRF52 DK should my RugRover shield be placed. 
shieldZOffset = 11.7;
// Offset my RugRover shield STL model to sit right above the nRF52 DK.
shieldXOffset = -0.25;
shieldYOffset = -16.0;



// Tight clearance.
clearanceTight = 0.2;
// Loose clearance.
clearanceLoose = 0.3;



// The diameter of the circular robot base.
baseDiameter = 160.0;
// The thickness of the circular robot base.
baseThickness = 5.0;
// The thickness of the motor mount.
motorMountThickness = 2.5;
// Clearance between robot base and wheel.
wheelClearance = 2.0;
// Additional clearance to have between caster wheel and edge of robot base.
casterClearance = 1.0;
// Clearance around the motor for the mount.
motorMountClearance = clearanceLoose;
// How much larger should the caster mount be than the caster plate itself.
casterMountClearance = 2.0;
// The radius of the rounded edges of the caster mount.
casterMountRadius = 1.0;
// Raise the cliff detctors by this amount to make room for the header pins
// sticking out the back of the PCB.
cliffDetectorMountThickness = 3.0;
// The amount of the cliff detector PCB to the left hanging off of the mount, where header
// pins are located.
cliffDetectorMountOffset = 2.54;
// Angles at which the 3 bumper switches should be placed around the robot base.
bumperSwitchAngles = [-25, 151, -151];
// How many degrees each bumper switch should be roated to get lever facing correct direction.
bumperSwitchFlips = [180, 0, 180];
// The length of the slots used to mount the buper switches onto the base.
bumperSwitchSlotLength = 11.5;
// Angles to locate the mounting holes for the bumper.
bumperMountAngles = [0, 120, -120];
// Offset of the bumper mounting holes from the outside diameter.
bumperMountOffset = 22.0;
// Bumper mounting hole diameters for M3 bolts.
bumperMountDiameter = 3.0 + clearanceLoose;
// Bumper mounting countersink hole size to allow access through caster mount block.
bumperMountCountersinkDiameter = 6.0;
// How far from the robot base should the nRF52DK PCB be mounted.
nRF52DK_MountingHeight = 6.0;
// Diameter of the hole used to attach standoffs for the nRF52DK PCB.
nRF52DK_MountingHoleDiameter = 3.0;
// Diameter of hole in middle of base for pulling cables through.
cableHoleDiameter = 25.0;
// Where the battery pack should be placed on the bottom of the bot, in the Y axis.
batteryYOffset = -38;
// Dimensions of slots used to place straps through to hold battery to underside of chassis.
batteryStrapSlotWidth = 2.5;
batteryStrapSlotLength = 5.0;
// The ratio of battery diameters to either side of the X center line, the battery strap 
// slots should be placed. 1.5 would put close to battery and larger pulls it out a bit.
batteryStrapSlotXRatio = 1.7;
// The extra amount to slide the battery strap slot down in the Y axis from the inside edge
// of the battery pack.
batteryStrapSlotYOffset = 12.0;
// Dimensions of ridges placed around battery pack to keep it from moving in X/Y plane.
batteryPackRidgeInsideLength = 10.0;
batteryPackRidgeOutsideLength = 20.0;
batteryPackRidgeWidth = 2.0;
batteryPackRidgeHeight = batteryDiameter/4;
batteryPackRidgeClearance = clearanceLoose;
// How much larger should the diameter of the bumper skirt be than the chassis.
bumperDiameterClearance = 4.0;
// How thick should the bumper skirt be?
// UNDONE: Will depend on slicer settings.
bumperThickness = 0.3 * 4;
// Thickness of the top of the  bumper skirt.
bumperTopThickness = 2.0;
// How far above the ground should the skirt be? Should be low enough to detect things that
// could hit battery pack, motors, etc.
bumperGroundClearance = 20.0;
// Diameter of flexible bumper standoffs.
bumperStandoffDiameter = 6.0;
// How tall are the flexible bumper standoffs.
bumperStandoffHeight = 43.0;
// The amount of extra top on the bumper skirt there should be to cover the flexible standoffs.
bumperTopClearance = 2.0;
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

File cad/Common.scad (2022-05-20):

/*  Copyright (C) 2022  Adam Green (https://github.com/adamgreen)

    This program is free software; you can redistribute it and/or
    modify it under the terms of the GNU General Public License
    as published by the Free Software Foundation; either version 2
    of the License, or (at your option) any later version.

    This program is distributed in the hope that it will be useful,
    but WITHOUT ANY WARRANTY; without even the implied warranty of
    MERCHANTABILITY or FITNESS FOR A PARTICULAR PURPOSE.  See the
    GNU General Public License for more details.
*/
// Variables and modules used to model the various parts of my RugRover bot.
include <ExternalParts.scad>

// ************
//  Parameters
// ************
// Tight clearance.
clearanceTight = 0.2;
// Loose clearance.
clearanceLoose = 0.3;


// The diameter of the circular robot base.
baseDiameter = 160.0;
// The thickness of the circular robot base.
baseThickness = 5.0;
// The thickness of the motor mount.
motorMountThickness = 2.5;
// Clearance between robot base and wheel.
wheelClearance = 2.0;
// Additional clearance to have between caster wheel and edge of robot base.
casterClearance = 1.0;
// Clearance around the motor for the mount.
motorMountClearance = clearanceLoose;
// How much larger should the caster mount be than the caster plate itself.
casterMountClearance = 2.0;
// The radius of the rounded edges of the caster mount.
casterMountRadius = 1.0;
// Raise the cliff detctors by this amount to make room for the header pins
// sticking out the back of the PCB.
cliffDetectorMountThickness = 3.0;
// The amount of the cliff detector PCB to the left hanging off of the mount, where header
// pins are located.
cliffDetectorMountOffset = 2.54;
// Angles at which the 3 bumper switches should be placed around the robot base.
bumperSwitchAngles = [-25, 151, -151];
// How many degrees each bumper switch should be roated to get lever facing correct direction.
bumperSwitchFlips = [180, 0, 180];
// The length of the slots used to mount the buper switches onto the base.
bumperSwitchSlotLength = 11.5;
// Angles to locate the mounting holes for the bumper.
bumperMountAngles = [0, 120, -120];
// Offset of the bumper mounting holes from the outside diameter.
bumperMountOffset = 22.0;
// Bumper mounting hole diameters for M3 bolts.
bumperMountDiameter = 3.0 + clearanceLoose;
// Bumper mounting countersink hole size to allow access through caster mount block.
bumperMountCountersinkDiameter = 6.0;
// How far from the robot base should the nRF52DK PCB be mounted.
nRF52DK_MountingHeight = 6.0;
// Diameter of the hole used to attach standoffs for the nRF52DK PCB.
nRF52DK_MountingHoleDiameter = 3.0;
// Diameter of hole in middle of base for pulling cables through.
cableHoleDiameter = 25.0;
// Where the battery pack should be placed on the bottom of the bot, in the Y axis.
batteryYOffset = -38;
// Dimensions of slots used to place straps through to hold battery to underside of chassis.
batteryStrapSlotWidth = 2.5;
batteryStrapSlotLength = 5.0;
// The ratio of battery diameters to either side of the X center line, the battery strap
// slots should be placed. 1.5 would put close to battery and larger pulls it out a bit.
batteryStrapSlotXRatio = 1.7;
// The extra amount to slide the battery strap slot down in the Y axis from the inside edge
// of the battery pack.
batteryStrapSlotYOffset = 12.0;
// Dimensions of ridges placed around battery pack to keep it from moving in X/Y plane.
batteryPackRidgeInsideLength = 10.0;
batteryPackRidgeOutsideLength = 20.0;
batteryPackRidgeWidth = 2.0;
batteryPackRidgeHeight = batteryDiameter/4;
batteryPackRidgeClearance = clearanceLoose;
// How much larger should the diameter of the bumper skirt be than the chassis.
bumperDiameterClearance = 4.0;
// How thick should the bumper skirt be?
// UNDONE: Will depend on slicer settings.
bumperThickness = 0.3 * 4;
// Thickness of the top of the  bumper skirt.
bumperTopThickness = 2.0;
// How far above the ground should the skirt be? Should be low enough to detect things that
// could hit battery pack, motors, etc.
bumperGroundClearance = 20.0;
// Diameter of flexible bumper standoffs.
bumperStandoffDiameter = 6.0;
// How tall are the flexible bumper standoffs.
bumperStandoffHeight = 43.0;
// The amount of extra top on the bumper skirt there should be to cover the flexible standoffs.
bumperTopClearance = 2.0;
// The desired diameter of the roll of tungsten to be placed at the back of the bot.
counterWeightDiameter = 16.0;
// The thickness of the holder to contain the roll of tungsten at the back of the bot.
counterWeightHolderThickness = 1.0;
// The ratio of the height of the holder to its width.
counterWeightHolderRatio = 2.0;
// The number of degrees that holder should take up at the back of the bot.
counterWeightHolderAngle = 100.0;
// The inside of the holder will be hollowed out this much less in degrees on either end.
counterWeightHolderInsideOffsetAngle = 1.0;
// Amount of clearance to place around bumper switch.
counterWeightHolderSwitchClearance = 2.5;
// Amount of clearance to place around flexible bumper standoff.
counterWeightHolderBumperHoleClearance = 5.0;




// *******************
//  Calculated Values
// *******************
// Determine the offset of the outside of the wheel needed to make sure that it is fully enclosed
// by the base.
encloseOffset = sqrt((baseDiameter/2)^2-(wheelDiameter/2)^2);
// Offset wheels so that they fall fully within the base.
wheelXOffset = encloseOffset-wheelThickness/2;
// Offset motors so that output shaft is flush with outside of wheel.
motorXOffset = encloseOffset-(motorGearboxCollarDepth+motorGearboxShaftLength);
// Motors should sit on top of the base.
motorZOffset = motorGearboxDiameter/2 + baseThickness;
// Offset wheels up off the base the same amount as the motors.
wheelZOffset = motorZOffset;
// Make sure that caster wheel stays within confines of body so that it never touches wrap around bumper.
casterYOffset = baseDiameter/2 - casterArmXOffset - casterDiameter/2 - casterClearance;
// Total caster height.
casterTotalHeight = casterPlateThickness + casterBearingHeight + casterArmZOffset + casterDiameter/2;
// Amount of wheel below the robot base.
wheelHeight = wheelDiameter/2 + wheelZOffset;
// How much taller is the caster in comparison to the drive wheels.
casterZOffset = wheelHeight - casterTotalHeight;
// Height of the casterMount.
casterMountHeight = casterZOffset - baseThickness;
// Inner diameter of the bumper skirt.
bumperID = baseDiameter + bumperDiameterClearance;
// Outer diameter of the bumper skirt.
bumperOD = bumperID + 2*bumperThickness;
// The Z offset where the bottom of the skirt should be.
bumperZOffset = wheelHeight - bumperGroundClearance;
// How tall should the bumper skirt be? Determined by ground clearance and standoff height.
bumperHeight = wheelHeight-bumperGroundClearance+bumperStandoffHeight;
// The diameter of the large hole in the top of the bumper skirt.
bumperTopID = baseDiameter-bumperMountOffset*2-bumperStandoffDiameter-2*bumperTopClearance;
// Outside width of the holder.
counterWeightHolderOutsideWidth = counterWeightDiameter + 2*counterWeightHolderThickness;
// Radius on the base on which the cylinder will be centered.
counterWeightHolderOffsetRadius = baseDiameter/2-counterWeightHolderOutsideWidth/2;




// Circular robot base with mounting for motors, caster, sensors, etc.
module base() {
    difference() {
        union() {
            cylinder(h=baseThickness, d=baseDiameter);
            motorMounts();
            casterMount();
            placeCliffDetectors()
                mountForCliffDetectors();
            batteryPackRidges();
        }
        // Things to remove from the circular base.
        wheelCutout(0);
        wheelCutout(1);
        casterMountHoles();
        placeCliffDetectors()
            holesForCliffDetectors();
        bumperSwitchCutouts();
        pcbMountHoles();
        cableHole();
        bumperMountHoles();
        batterySlotCutouts();
    }
}

// Cutout slots on the side to fit the wheels.
module wheelCutout(leftWheel) {
    xOffset = baseDiameter/4+encloseOffset-wheelThickness-wheelClearance;
    rotate([0, 0, leftWheel * 180.0])
        translate([xOffset, 0, baseThickness/2])
            cube([baseDiameter/2, wheelDiameter+2*wheelClearance, baseThickness+0.02], center=true);
}

module motorMounts() {
    motorMount();
    rotate([0, 0, 180]) motorMount();
}

// Vertical motor mount with holes for gearbox collar, output shaft, and screw holes.
module motorMount() {
    xOffset = motorXOffset+motorMountThickness/2;
    mountWidth = motorGearboxDiameter + 2*motorMountClearance + 2*motorMountThickness;
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

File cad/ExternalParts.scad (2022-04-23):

/*  Copyright (C) 2022  Adam Green (https://github.com/adamgreen)

    This program is free software; you can redistribute it and/or
    modify it under the terms of the GNU General Public License
    as published by the Free Software Foundation; either version 2
    of the License, or (at your option) any later version.

    This program is distributed in the hope that it will be useful,
    but WITHOUT ANY WARRANTY; without even the implied warranty of
    MERCHANTABILITY or FITNESS FOR A PARTICULAR PURPOSE.  See the
    GNU General Public License for more details.
*/
// Models for external parts from Pololu, Adafruit, etc to be mounted on RugRover bot.


// Motor part dimensions.
//  Gearbox built in 3 pieces where piece separation is represented by 2 rings in this  model.
//  Also has 2 tapped holes for mounting. It also includes the output D-shaft and the collar
//  where the output shaft enters the gearbox.
motorGearboxDiameter = 20.0;
motorGearboxLength = 17.3;
motorGearboxRingOffset = 3.0;
motorGearboxRingWidth = 0.1;
motorGearboxRingDepth = 0.1;
motorGearboxHoleOuter = 17.08;
motorGearboxHoleInner = 12.86;
motorGearboxHoleDiameter = 2.5;     //(motorGearboxHoleOuter - motorGearboxHoleInner)/2;
motorGearboxHoleOffsetRadius = 7.5; //(motorGearboxHoleOuter + motorGearboxHoleInner)/2/2;
motorGearboxHoleDepth = 2.0;
motorGearboxCollarDiameter = 7.0;
motorGearboxCollarDepth = 3.0;
motorGearboxShaftDiameter = 4.0;
motorGearboxShaftIndentDiameter = 3.5;
motorGearboxShaftLength = 14.5;
//  The electric motor attached to the back of the gearbox. Includes shaft sticking out the back
//  along with the electrical connections.
motorDiameter = motorGearboxDiameter;
motorFlatWidth = 15.4;
motorLength = 25.0;
motorCollarDiameter = 6.05;
motorCollarDepth = 1.9-0.7;
motorShaftDiameter = 2.0;
motorShaftLength = 6.0;

// Wheel dimensions.
wheelDiameter = 80.65;
wheelThickness = 10.0;

// Caster dimensions.
//  The wheel itself.
casterDiameter = 29.85;
casterInnerDiameter = 22.40;
casterThickness = 13.2;
casterInnerThickness = casterThickness - 2 * 5.25;
//  The plate which has the thrust bearing and attaches to the bot body.
casterPlateWidth = 38.2;
casterPlateHeight = 31.95;
casterPlateThickness = 1.3;
//  Placement of 4 holes used to mount plate to bot body.
casterHoleDiameter = 4.1;
casterHoleXSpacing = (33.65 + 25.2) / 2;
casterHoleYSpacing = (18.88 + 27.15) / 2;
//  Thrust bearing between plate and arm that holds the wheel.
casterBearingTopDiameter = 28.42;
casterBearingBottomDiameter = 23.0;
casterBearingHeight = 4.1 - casterPlateThickness;
//  Arm that holds the wheel.
casterArmTopDiameter = 25.55;
casterArmBottomRadius = 10.0 / 2;
casterArmBottomWidth = 18.0;
casterArmTopZOffset = 1.0;
casterArmXOffset = 10.0;
casterArmZOffset = 25.0;
casterArmCutoutTopThickness = 1.2;
casterArmCutoutTopWidth1 = 17.4;
casterArmCutoutTopWidth2 = 22.0;
casterArmCutoutBottomWidth = 15.0;

// Dimensions of the VL6180X based cliff detector.
cliffDetectorWidth = 12.7;
cliffDetectorHeight = 17.8;
cliffDetectorMountingHoleDiameter = 2.2;
cliffDetectorMountingHoleXOffset = cliffDetectorWidth - 2.5;
cliffDetectorMountingHoleYOffset = cliffDetectorHeight/2 - 2.5;

// Rough dimensions of bumper switches.
bumperSwitchWidth = 19.8;
bumperSwitchHeight = 10.6;
bumperSwitchThickness = 6.2;
bumperSwitchHoleDiameter = 2.5;
bumperSwitchHoleXOffset = 9.5/2;
bumperSwitchHoleYOffset = -bumperSwitchHeight/2 + 2.9;

// Dimensions of the Nordic nRF52DK PCB.
nRF52DK_Length = 101.6;
nRF52DK_Width = 63.5;
nRF52DK_Thickness = 1.6;
// Location of the mounting holes in the nRF52DK PCB.
nRF52DK_MountingHoles=[[15.24, 50.8+5, 0], [13.97, 2.54+5, 0], [66, 7.62+5, 0], [66, 35.56+5, 0], [96.52, 2.54+5, 0]];

// Dimensions of the AA cells in the Pololu battery packs.
batteryDiameter = 14.6;
batteryLength = 50.4;

// Dimensions of my RugRover shield that to be placed on top of the nRF52 DK.
// How much further above the nRF52 DK should my RugRover shield be placed.
shieldZOffset = 11.7;
// Offset my RugRover shield STL model to sit right above the nRF52 DK.
shieldXOffset = -0.25;
shieldYOffset = -16.0;



// Pololu's Metal Gearmotor 20Dx43L mm 6V CB with Extended Motor Shaft
// https://www.pololu.com/category/214/6v-carbon-brush-cb-20d-gearmotors
// The face of the gearbox is at the origin.
module motor() {
    translate([-motorGearboxLength, 0, 0]) {
        motorGearbox();
        motorMotor();
    }
}

module motorGearbox() {
    translate([motorGearboxLength/2, 0, 0]) {
        rotate([0, 90, 0]) {
            difference() {
                cylinder(h=motorGearboxLength, d=motorGearboxDiameter, center=true);
                motorGearboxRing(1.0);
                motorGearboxRing(-1.0);
                motorGearboxMountingHoles(1.0);
                motorGearboxMountingHoles(-1.0);
            }
            motorGearboxCollar();
            motorGearboxShaft();
        }
    }
}

module motorGearboxRing(offset) {
    offsetFromCenter = offset* (motorGearboxLength/2 - motorGearboxRingOffset);
    translate([0, 0, offsetFromCenter]) {
        difference() {
            cylinder(h=motorGearboxRingWidth, d=motorGearboxDiameter+0.002, center=true);
            cylinder(h=motorGearboxRingWidth+0.002, d=motorGearboxDiameter-motorGearboxRingDepth, center=true);
        }
    }
}

module motorGearboxMountingHoles(offset) {
    translate([0, offset*motorGearboxHoleOffsetRadius, motorGearboxLength/2])
        cylinder(h=motorGearboxHoleDepth*2, d=motorGearboxHoleDiameter, center=true);
}

module motorGearboxCollar() {
    translate([0, 0, motorGearboxLength/2])
        cylinder(h=motorGearboxCollarDepth*2, d=motorGearboxCollarDiameter, center=true);
}

module motorGearboxShaft() {
    translate([0, 0, motorGearboxLength/2 + motorGearboxCollarDepth]) {
        difference() {
            cylinder(h=motorGearboxShaftLength, d=motorGearboxShaftDiameter);
            translate([0, motorGearboxShaftDiameter/2+motorGearboxShaftIndentDiameter/2, motorGearboxShaftLength/2])
                cube([motorGearboxShaftDiameter, motorGearboxShaftDiameter, motorGearboxShaftLength+0.02], center=true);
        }
    }
}

module motorMotor() {
    translate([-motorLength/2, 0, 0]) {
        rotate([0, -90, 0]) {
            difference() {
                cylinder(h=motorLength, d=motorDiameter, center=true);
                motorFlat(1.0);
                motorFlat(-1.0);
            }
            motorBackCollar();
            motorBackShaft();
        }
    }
}

module motorFlat(offset) {
    translate([offset*(motorDiameter/2+motorFlatWidth/2), 0, 0])
        cube([motorDiameter, motorDiameter+0.02, motorLength+0.02], center=true);
}
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

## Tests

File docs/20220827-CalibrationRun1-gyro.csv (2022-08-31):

temperature | x | y | z
5.4635 | -8.588666666666667 | -8.7715 | 37.647333333333336
7.518666666666666 | -4.564666666666667 | -24.136833333333332 | 56.875166666666665
8.975833333333334 | 11.109833333333333 | -26.908666666666665 | 62.89366666666667
9.920666666666667 | 21.390166666666666 | -30.596666666666668 | 67.6595
10.357 | 25.501333333333335 | -33.42483333333333 | 68.62533333333333
10.994833333333334 | 23.9105 | -36.3595 | 68.3125
11.219666666666667 | 19.463666666666665 | -39.001333333333335 | 67.43
11.931333333333333 | 24.481166666666667 | -43.861666666666665 | 66.88816666666666
11.999833333333333 | 54.480333333333334 | -47.69683333333333 | 65.80216666666666
12.002333333333333 | 86.36483333333334 | -57.41916666666667 | 64.763
12.2135 | 108.60716666666667 | -31.237333333333332 | 61.10366666666667
12.852 | 86.38266666666667 | 5.012 | 51.3395
12.998 | 58.43366666666667 | 12.737 | 48.541666666666664
13.009166666666667 | 10.097 | 18.564166666666665 | 38.80016666666667
13.468833333333333 | 5.546166666666666 | 14.768333333333333 | 37.735166666666665
13.9615 | 2.4976666666666665 | 16.02316666666667 | 35.60033333333333
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

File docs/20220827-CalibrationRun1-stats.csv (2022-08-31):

accelX | accelY | accelZ | magX | magY | magZ | gryoX | gyroY | gyroZ | gyroTemperature
Mean: 216.80083333333334 | -351.4651666666667 | 4197.436166666666 | -146.698 | 38.809 | -846.3095 | -8.588666666666667 | -8.7715 | 37.647333333333336 | 5.4635
Variance: 25.902816441629824 | 17.353678918715456 | 39.665536228389136 | 28.96328988164579 | 29.173047841306893 | 64.81617911320207 | 665.6850857365116 | 299.6128898983164 | 276.21166149913864 | 0.7277890481746939
Mean: 217.3255 | -348.9705 | 4195.503333333333 | -146.12066666666666 | 39.93683333333333 | -846.8733333333333 | -4.564666666666667 | -24.136833333333332 | 56.875166666666665 | 7.518666666666666
Variance: 23.378779546591336 | 17.422866894475895 | 49.81795854881657 | 31.13962949380455 | 29.711795271434056 | 54.59372117579391 | 716.9159708840363 | 331.72506414958053 | 276.1026004056233 | 0.2763642829360418
Mean: 217.31383333333332 | -346.80216666666666 | 4193.695333333333 | -143.0605 | 36.45516666666666 | -846.5155 | 11.109833333333333 | -26.908666666666665 | 62.89366666666667 | 8.975833333333334
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

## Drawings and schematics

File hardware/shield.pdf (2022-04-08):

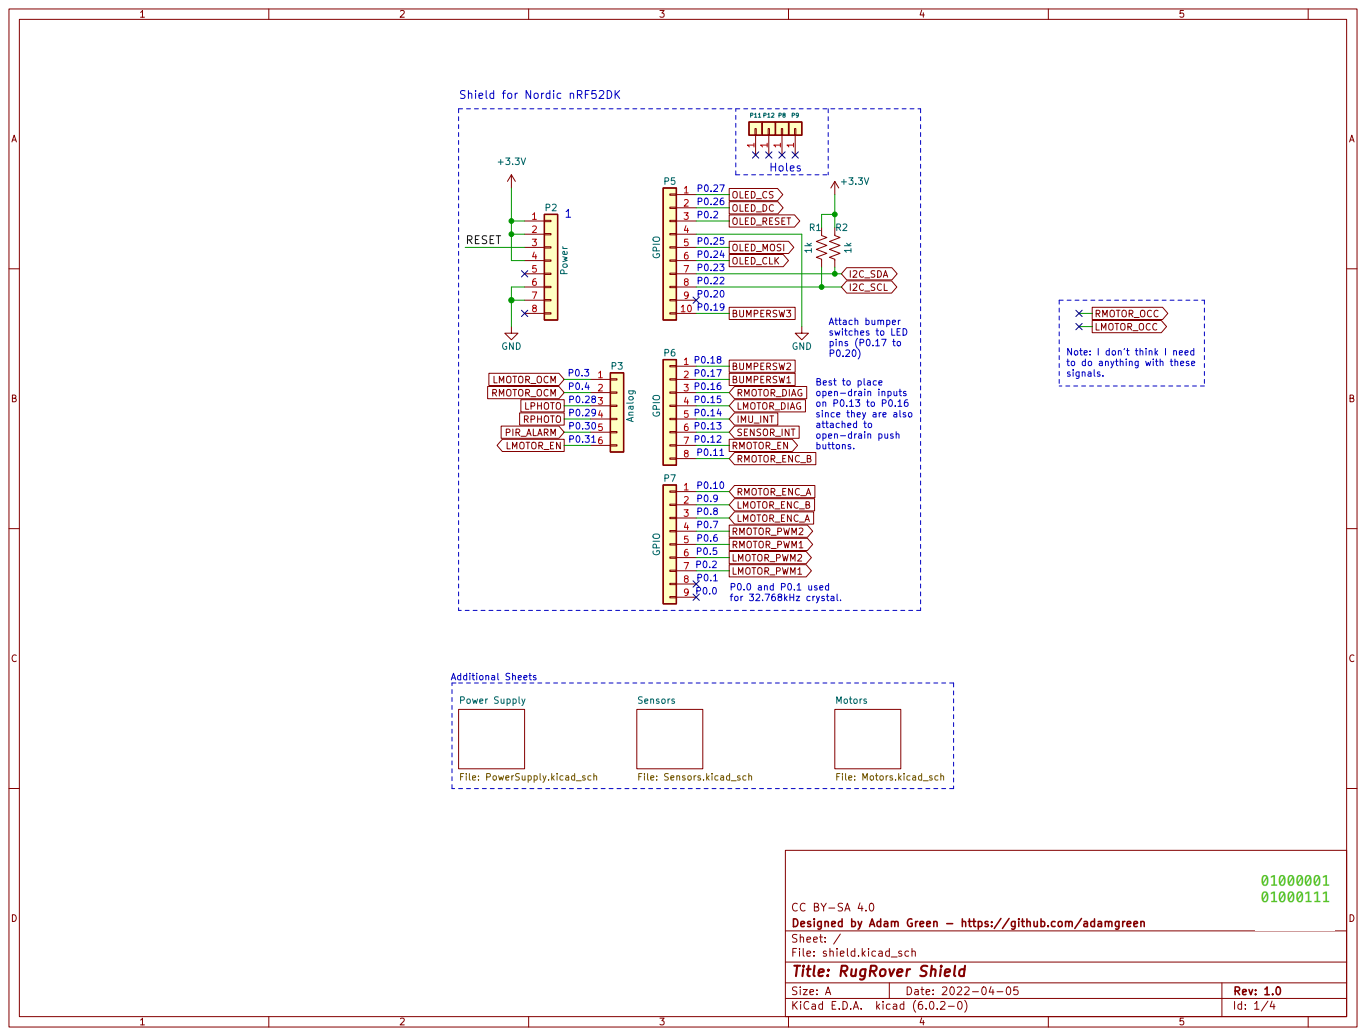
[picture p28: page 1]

Attach bumper switches to LED pins (P0.17 to

to do anything with these

File: shield.kicad_sch Sheet: / Designed by Adam Green - https://github.com/adamgreen CC BY-SA 4.0 Motors File: Motors.kicad_sch Power Supply

Id: 1/4 Title: RugRover Shield

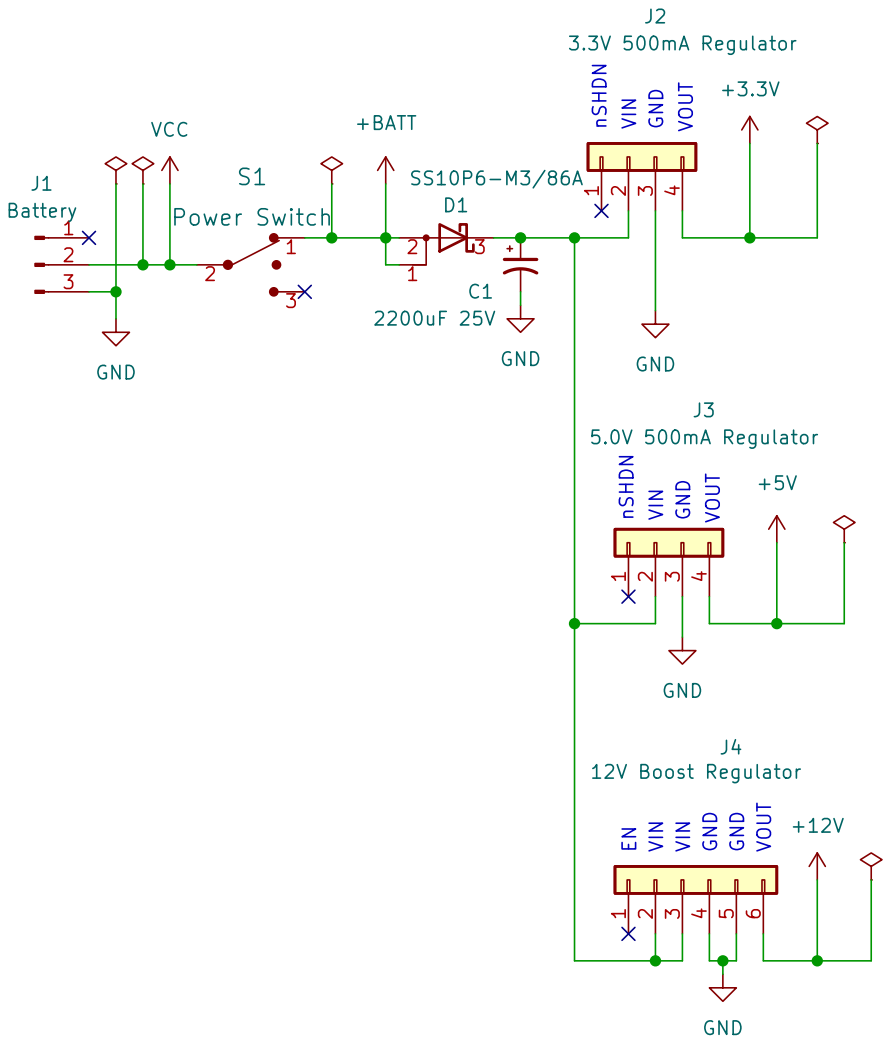
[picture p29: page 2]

3.3V 500mA Regulator +3.3V
12V Boost Regulator GND GND nSHDN ENVIN VIN GND VOUT VIN GND GND VOUT nSHDN VIN GND VOUT

Designed by Adam Green - https://github.com/adamgreen CC BY-SA 4.0
Sheet: /Power Supply/
File: PowerSupply.kicad_sch
Id: 2/4 Title: RugRover Shield

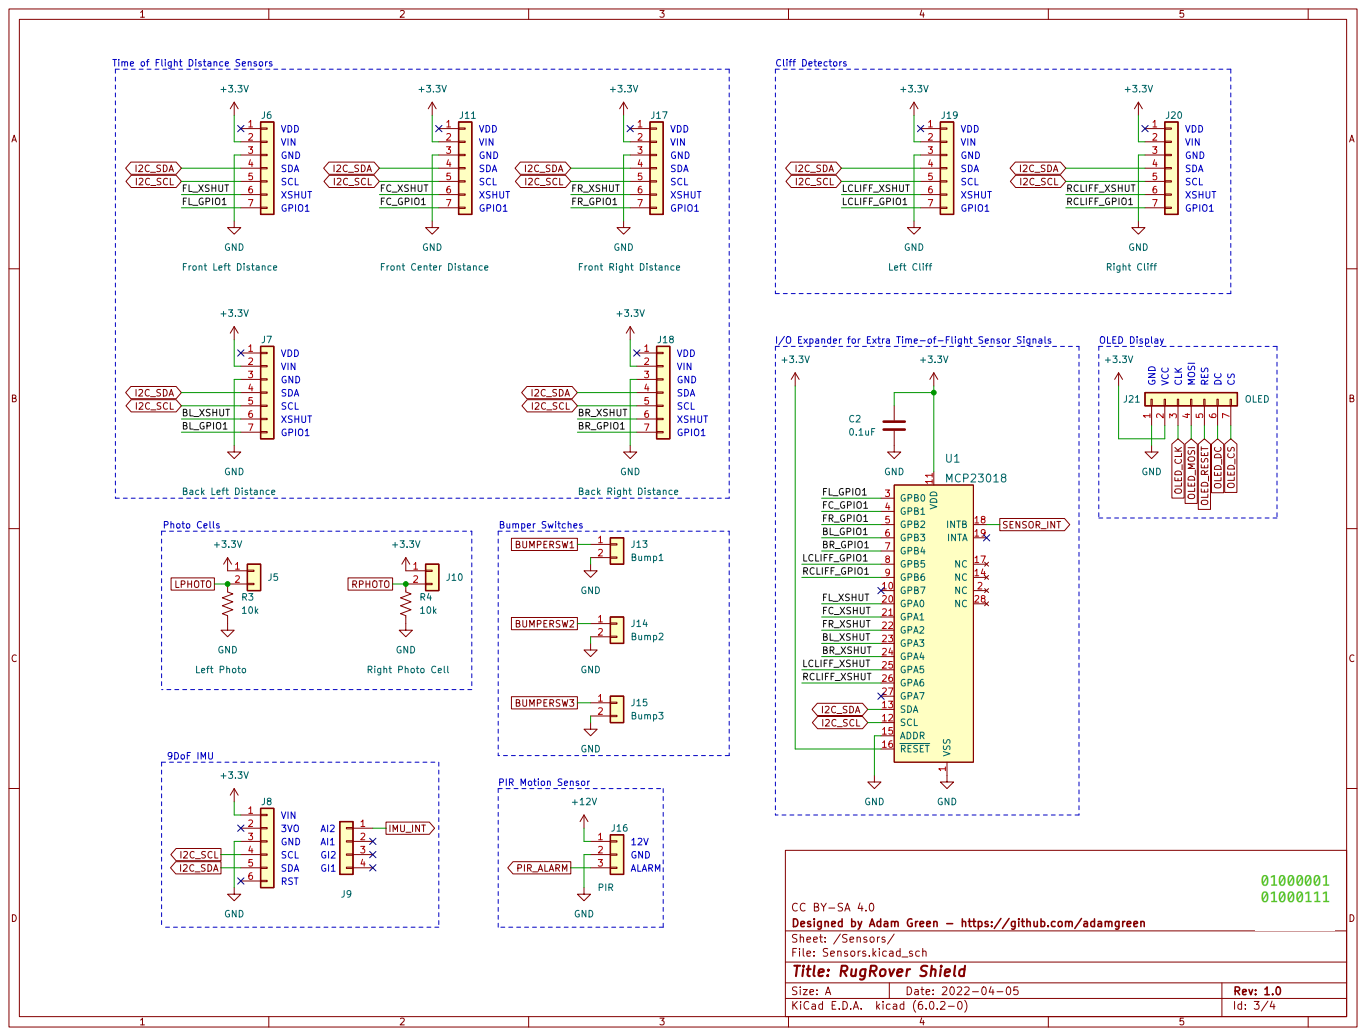
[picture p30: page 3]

J18 Back Right Distance GND

1 GPB7 10 VDD 11 SCL 12 SDA 13 NC 14 ADDR 15 ~{RESET} 16 NC 17

File: Sensors.kicad_sch Sheet: /Sensors/ Designed by Adam Green - https://github.com/adamgreen CC BY-SA 4.0

Id: 3/4 Title: RugRover Shield

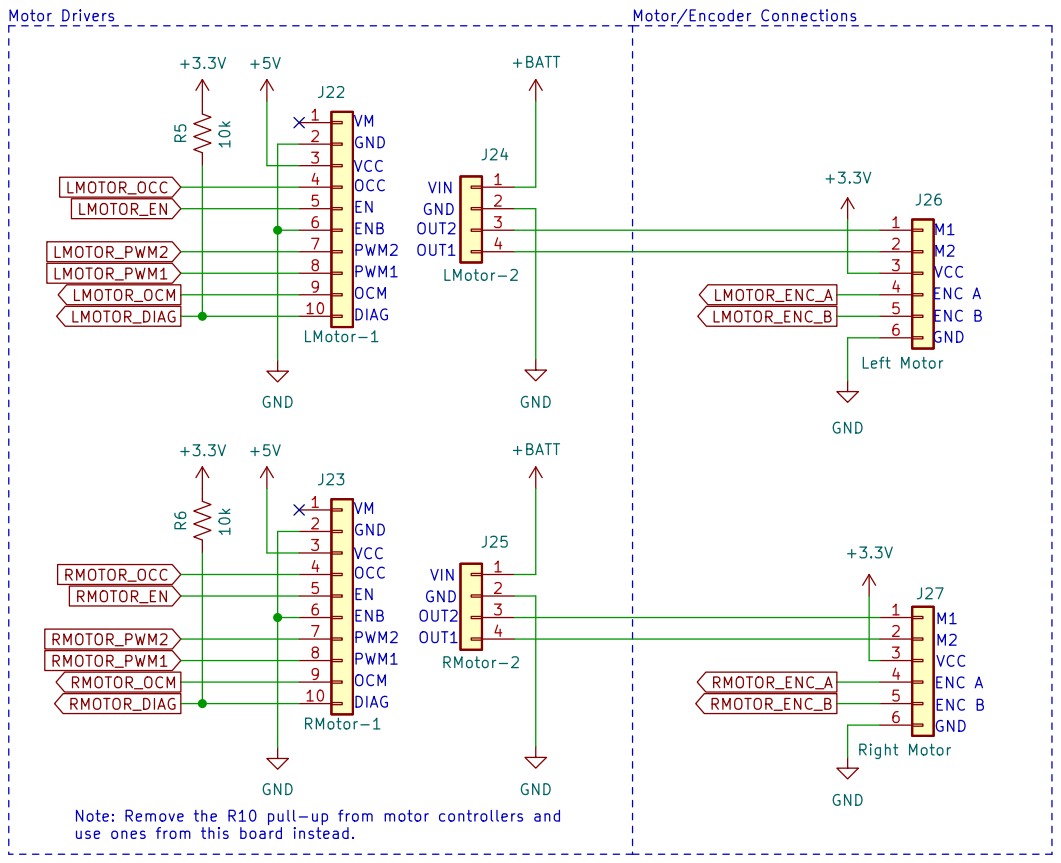
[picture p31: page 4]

ENC B GND M2 M1 Motor/Encoder Connections PWM2 DIAG

+BATT | 3

LMotor-2 GND GND GND

File: Motors.kicad_sch Sheet: /Motors/ Designed by Adam Green - https://github.com/adamgreen CC BY-SA 4.0

Id: 4/4 Title: RugRover Shield

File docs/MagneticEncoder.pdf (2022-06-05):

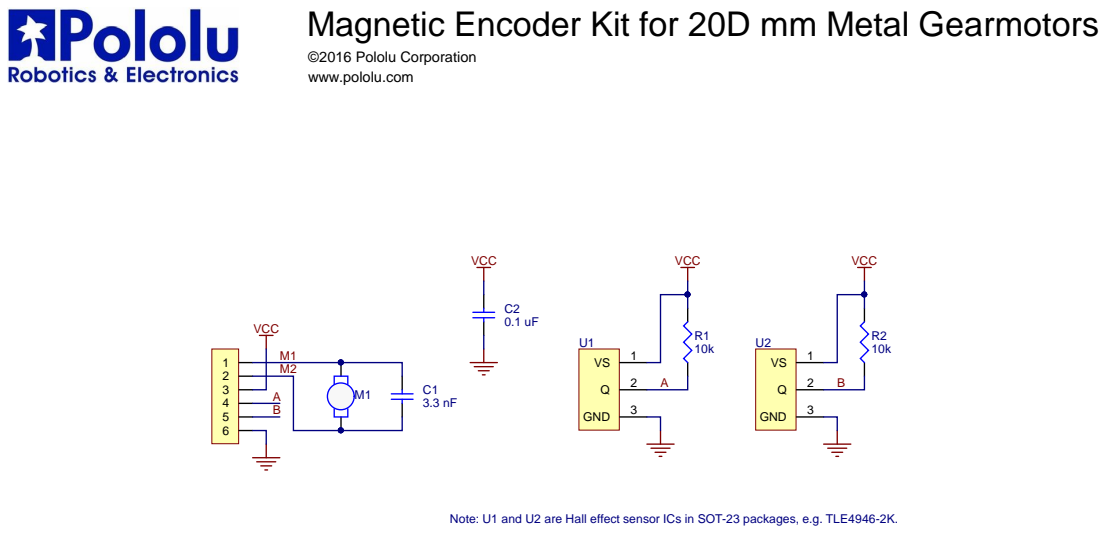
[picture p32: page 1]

Magnetic Encoder Kit for 20D

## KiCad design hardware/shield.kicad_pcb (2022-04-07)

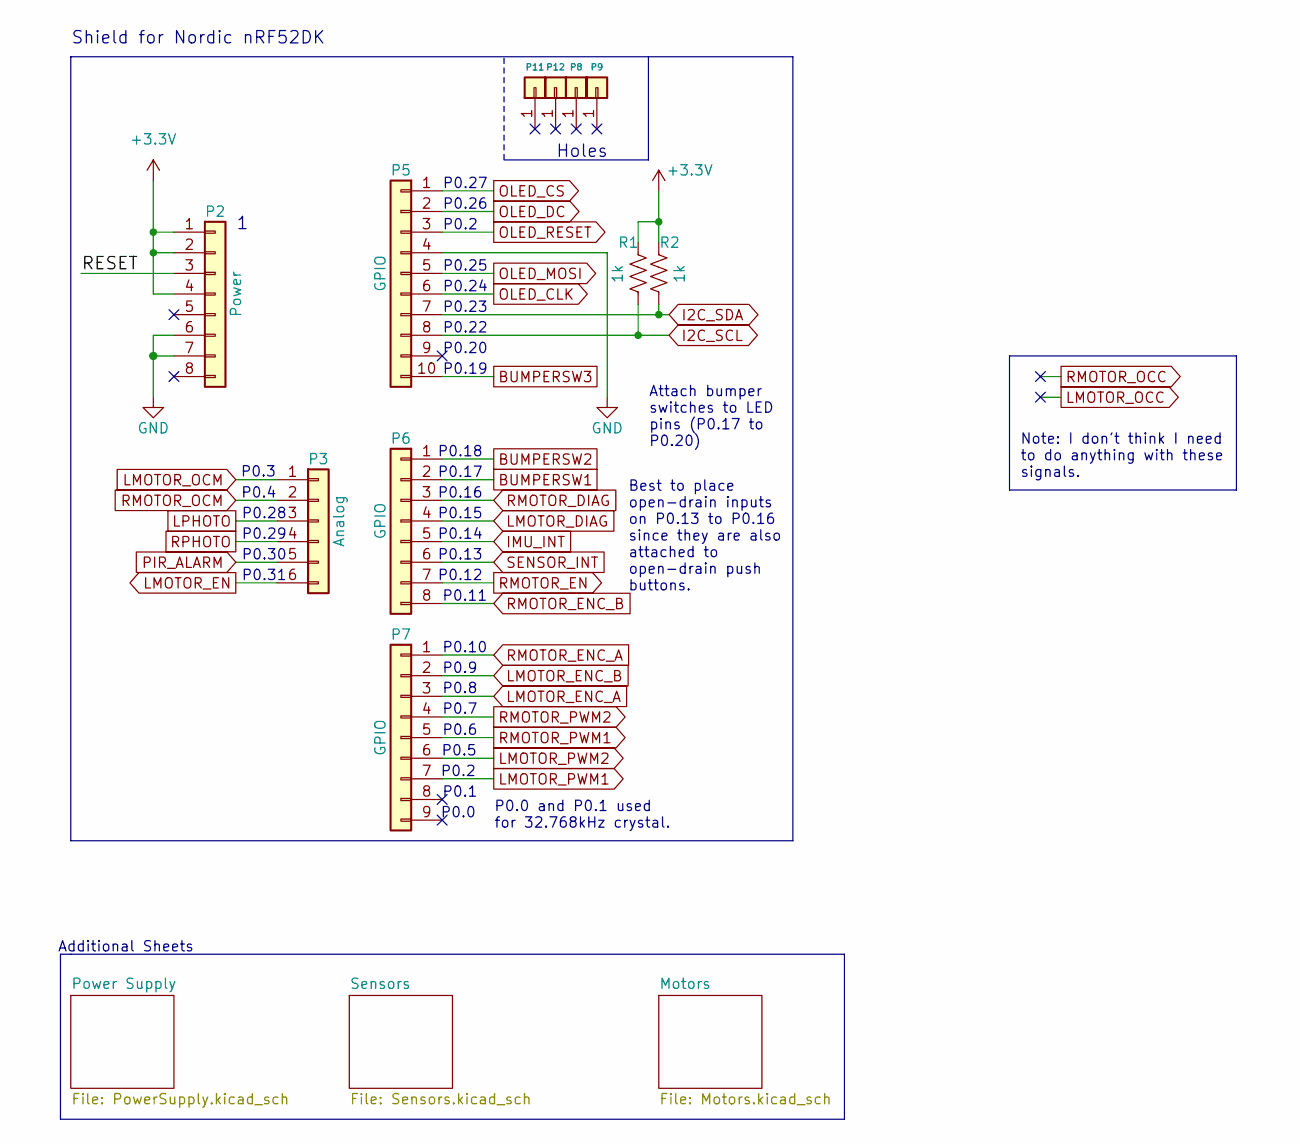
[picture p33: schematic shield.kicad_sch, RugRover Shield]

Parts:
P2: Power; PinHeader_1x08_P2.54mm_Vertical
P3: Analog; PinHeader_1x06_P2.54mm_Vertical
P5: GPIO; PinHeader_1x10_P2.54mm_Vertical
P6: GPIO; PinHeader_1x08_P2.54mm_Vertical
P7: GPIO; PinHeader_1x09_P2.54mm_Vertical
P8, P9, P11, P12: CONN_01X01; Arduino_1pin
R1, R2: 1k; R_0805_2012Metric_Pad1.20x1.40mm_HandSolder

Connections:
+3V3: P2.1, P2.2, P2.4, R1.1, R2.1; also elsewhere on the board
/RESET: P2.3
BUMPERSW1: P6.2; also elsewhere on the board
BUMPERSW2: P6.1; also elsewhere on the board
BUMPERSW3: P5.10; also elsewhere on the board
GND: P2.6, P2.7, P5.4; also elsewhere on the board
I2C_SCL: P5.8, R1.2; also elsewhere on the board
I2C_SDA: P5.7, R2.2; also elsewhere on the board
IMU_INT: P6.5; also elsewhere on the board
LMOTOR_DIAG: P6.4; also elsewhere on the board
LMOTOR_EN: P3.6; also elsewhere on the board
LMOTOR_ENC_A: P7.3; also elsewhere on the board
LMOTOR_ENC_B: P7.2; also elsewhere on the board
LMOTOR_OCM: P3.1; also elsewhere on the board
LMOTOR_PWM1: P7.7; also elsewhere on the board
LMOTOR_PWM2: P7.6; also elsewhere on the board
LPHOTO: P3.3; also elsewhere on the board
OLED_CLK: P5.6; also elsewhere on the board
OLED_CS: P5.1; also elsewhere on the board
OLED_DC: P5.2; also elsewhere on the board
OLED_MOSI: P5.5; also elsewhere on the board
OLED_RESET: P5.3; also elsewhere on the board
PIR_ALARM: P3.5; also elsewhere on the board
RMOTOR_DIAG: P6.3; also elsewhere on the board
RMOTOR_EN: P6.7; also elsewhere on the board
RMOTOR_ENC_A: P7.1; also elsewhere on the board
RMOTOR_ENC_B: P6.8; also elsewhere on the board
RMOTOR_OCM: P3.2; also elsewhere on the board
RMOTOR_PWM1: P7.5; also elsewhere on the board
RMOTOR_PWM2: P7.4; also elsewhere on the board
RPHOTO: P3.4; also elsewhere on the board
SENSOR_INT: P6.6; also elsewhere on the board

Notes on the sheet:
P0.24
P0.11
Attach bumper switches to LED pins (P0.17 to P0.20)
P0.14
P0.9
Note: I don't think I need to do anything with these signals.
P0.19
P0.12
P0.22
P0.30
P0.18
P0.5
P0.2
P0.20
Best to place open-drain inputs on P0.13 to P0.16 since they are also attached to open-drain push buttons.
P0.6
P0.23
P0.16
P0.17
P0.0 and P0.1 used for 32.768kHz crystal.
P0.4
P0.1
P0.31
P0.27
P0.15
P0.26
P0.3
P0.29
P0.8
P0.7
Holes
P0.13
P0.10
Additional Sheets
P0.25
P0.0
P0.28
Shield for Nordic nRF52DK

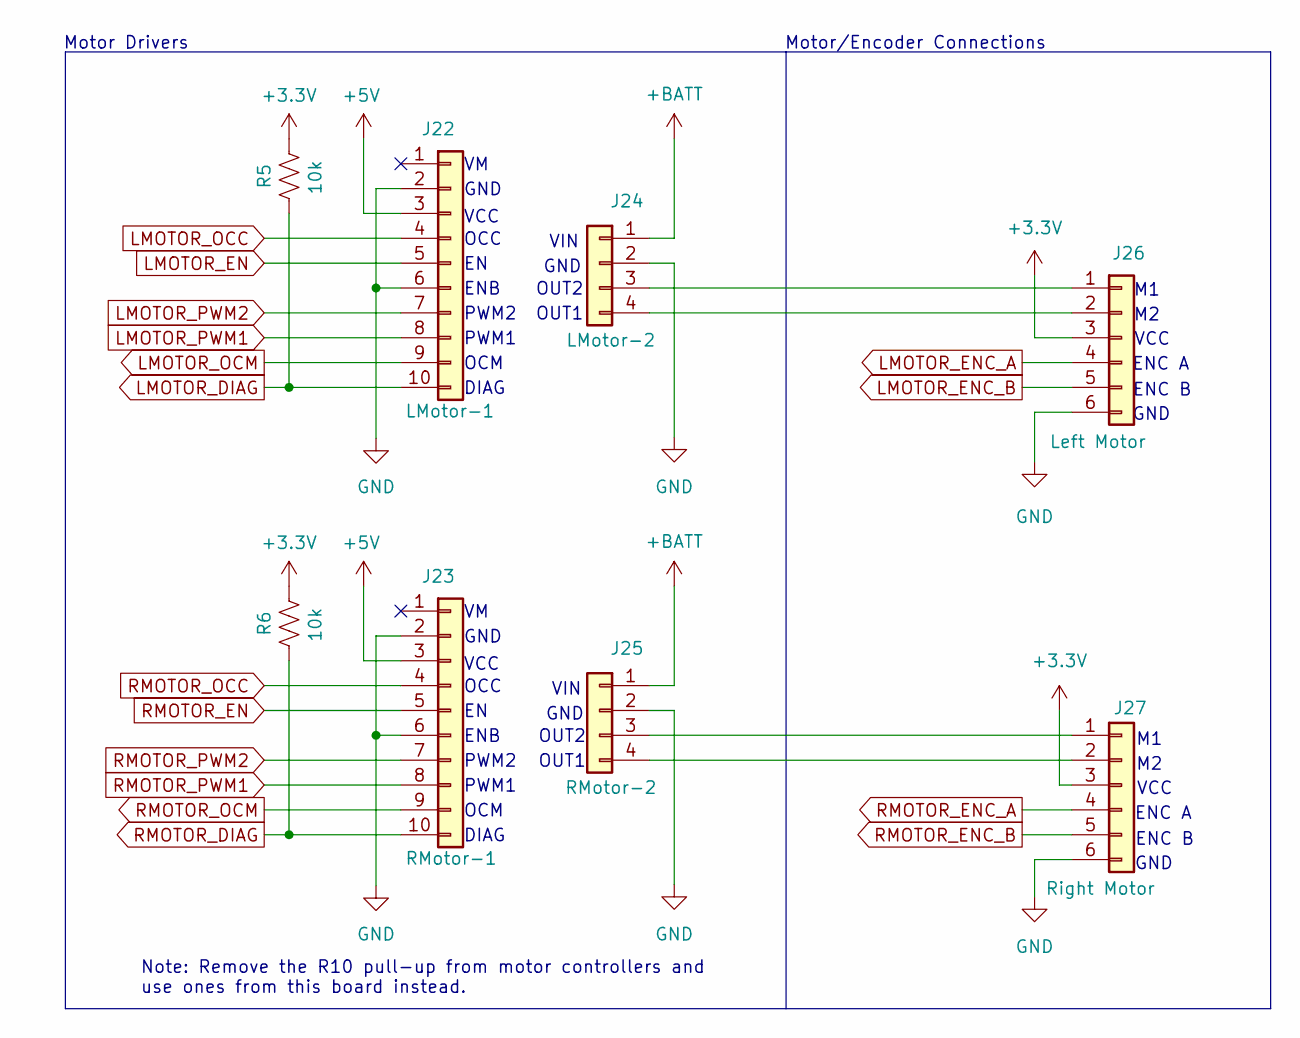
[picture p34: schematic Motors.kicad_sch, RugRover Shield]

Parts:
J22: LMotor-1; PinSocket_1x10_P2.54mm_Vertical
J23: RMotor-1; PinSocket_1x10_P2.54mm_Vertical
J24: LMotor-2; PinSocket_1x04_P2.54mm_Vertical
J25: RMotor-2; PinSocket_1x04_P2.54mm_Vertical
J26: Left Motor; PinSocket_1x06_P2.54mm_Horizontal
J27: Right Motor; PinSocket_1x06_P2.54mm_Horizontal
R5, R6: 10k; R_0805_2012Metric_Pad1.20x1.40mm_HandSolder

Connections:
+3V3: J26.3, J27.3, R5.2, R6.2; also elsewhere on the board
+5V: J22.3, J23.3; also elsewhere on the board
+BATT: J24.1, J25.1; also elsewhere on the board
GND: J22.2, J22.6, J23.2, J23.6, J24.2, J25.2, J26.6, J27.6; also elsewhere on the board
LMOTOR_DIAG: J22.10, R5.1; also elsewhere on the board
LMOTOR_EN: J22.5; also elsewhere on the board
LMOTOR_ENC_A: J26.4; also elsewhere on the board
LMOTOR_ENC_B: J26.5; also elsewhere on the board
LMOTOR_OCC: J22.4
LMOTOR_OCM: J22.9; also elsewhere on the board
LMOTOR_PWM1: J22.8; also elsewhere on the board
LMOTOR_PWM2: J22.7; also elsewhere on the board
unnamed: J24.3, J26.1
unnamed: J24.4, J26.2
unnamed: J25.3, J27.1
unnamed: J25.4, J27.2
RMOTOR_DIAG: J23.10, R6.1; also elsewhere on the board
RMOTOR_EN: J23.5; also elsewhere on the board
RMOTOR_ENC_A: J27.4; also elsewhere on the board
RMOTOR_ENC_B: J27.5; also elsewhere on the board
RMOTOR_OCC: J23.4
RMOTOR_OCM: J23.9; also elsewhere on the board
RMOTOR_PWM1: J23.8; also elsewhere on the board
RMOTOR_PWM2: J23.7; also elsewhere on the board

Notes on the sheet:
GND
OUT2
ENC A
PWM2
DIAG
VCC
ENB
ENC B
PWM1
Note: Remove the R10 pull-up from motor controllers and use ones from this board instead.
VIN
Motor Drivers
OUT1
OCC
Motor/Encoder Connections
OCM

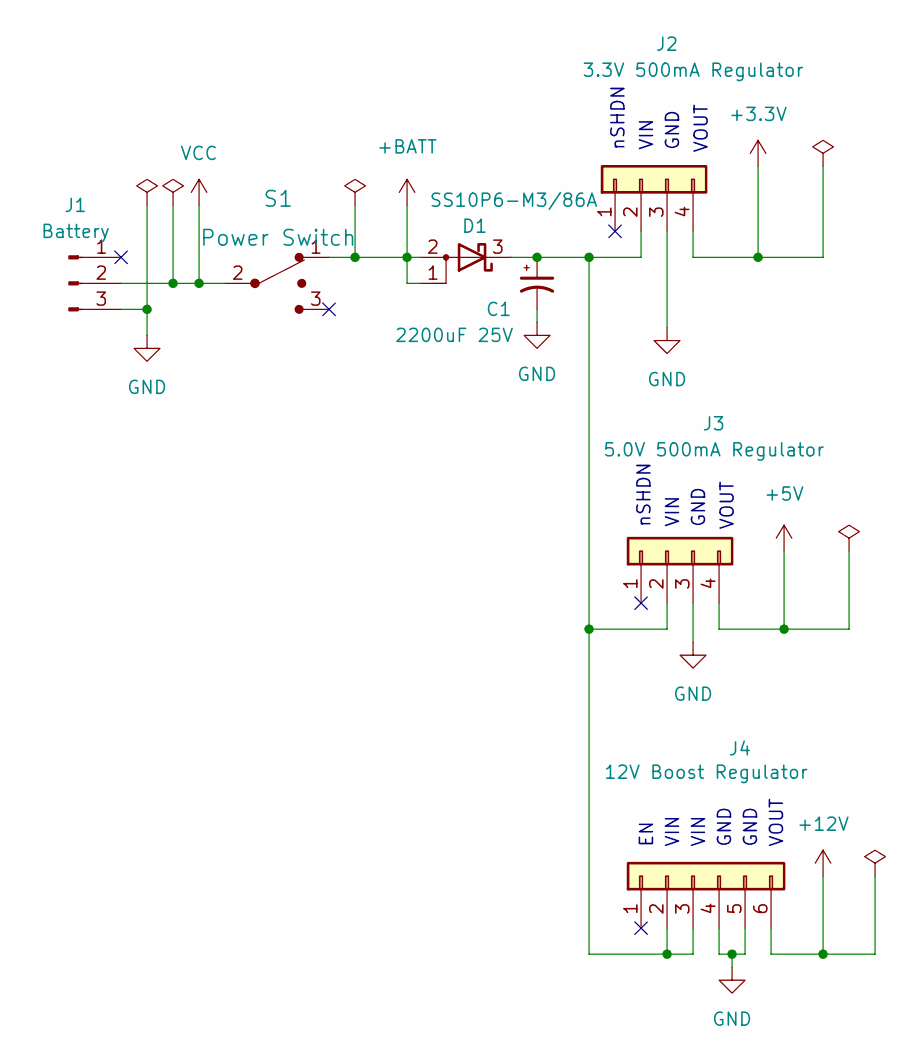
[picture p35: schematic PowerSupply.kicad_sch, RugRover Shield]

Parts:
C1: 2200uF 25V; CP_Radial_D13.0mm_P5.00mm
D1: SS10P6-M3/86A; TO-277A
J1: Battery; PinHeader_1x03_P2.54mm_Horizontal
J2: 3.3V 500mA Regulator; PinSocket_1x04_P2.54mm_Vertical
J3: 5.0V 500mA Regulator; PinSocket_1x04_P2.54mm_Vertical
J4: 12V Boost Regulator; PinSocket_1x06_P2.54mm_Vertical
S1: Power Switch; Toggle_Switch_100SP1T1B4M2QE; MPN 100SP1T1B4M2QE; Digi-Key_PN EG2355-ND

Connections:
+3V3: J2.4; also elsewhere on the board
+5V: J3.4; also elsewhere on the board
+12V: J4.6; also elsewhere on the board
+BATT: D1.1 (A), D1.2 (A), S1.1; also elsewhere on the board
GND: C1.2, J1.3, J2.3, J3.3, J4.4, J4.5; also elsewhere on the board
unnamed: C1.1, D1.3 (K), J2.2, J3.2, J4.2, J4.3
VCC: J1.2, S1.2 (Com)

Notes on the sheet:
VIN
GND
VOUT
nSHDN

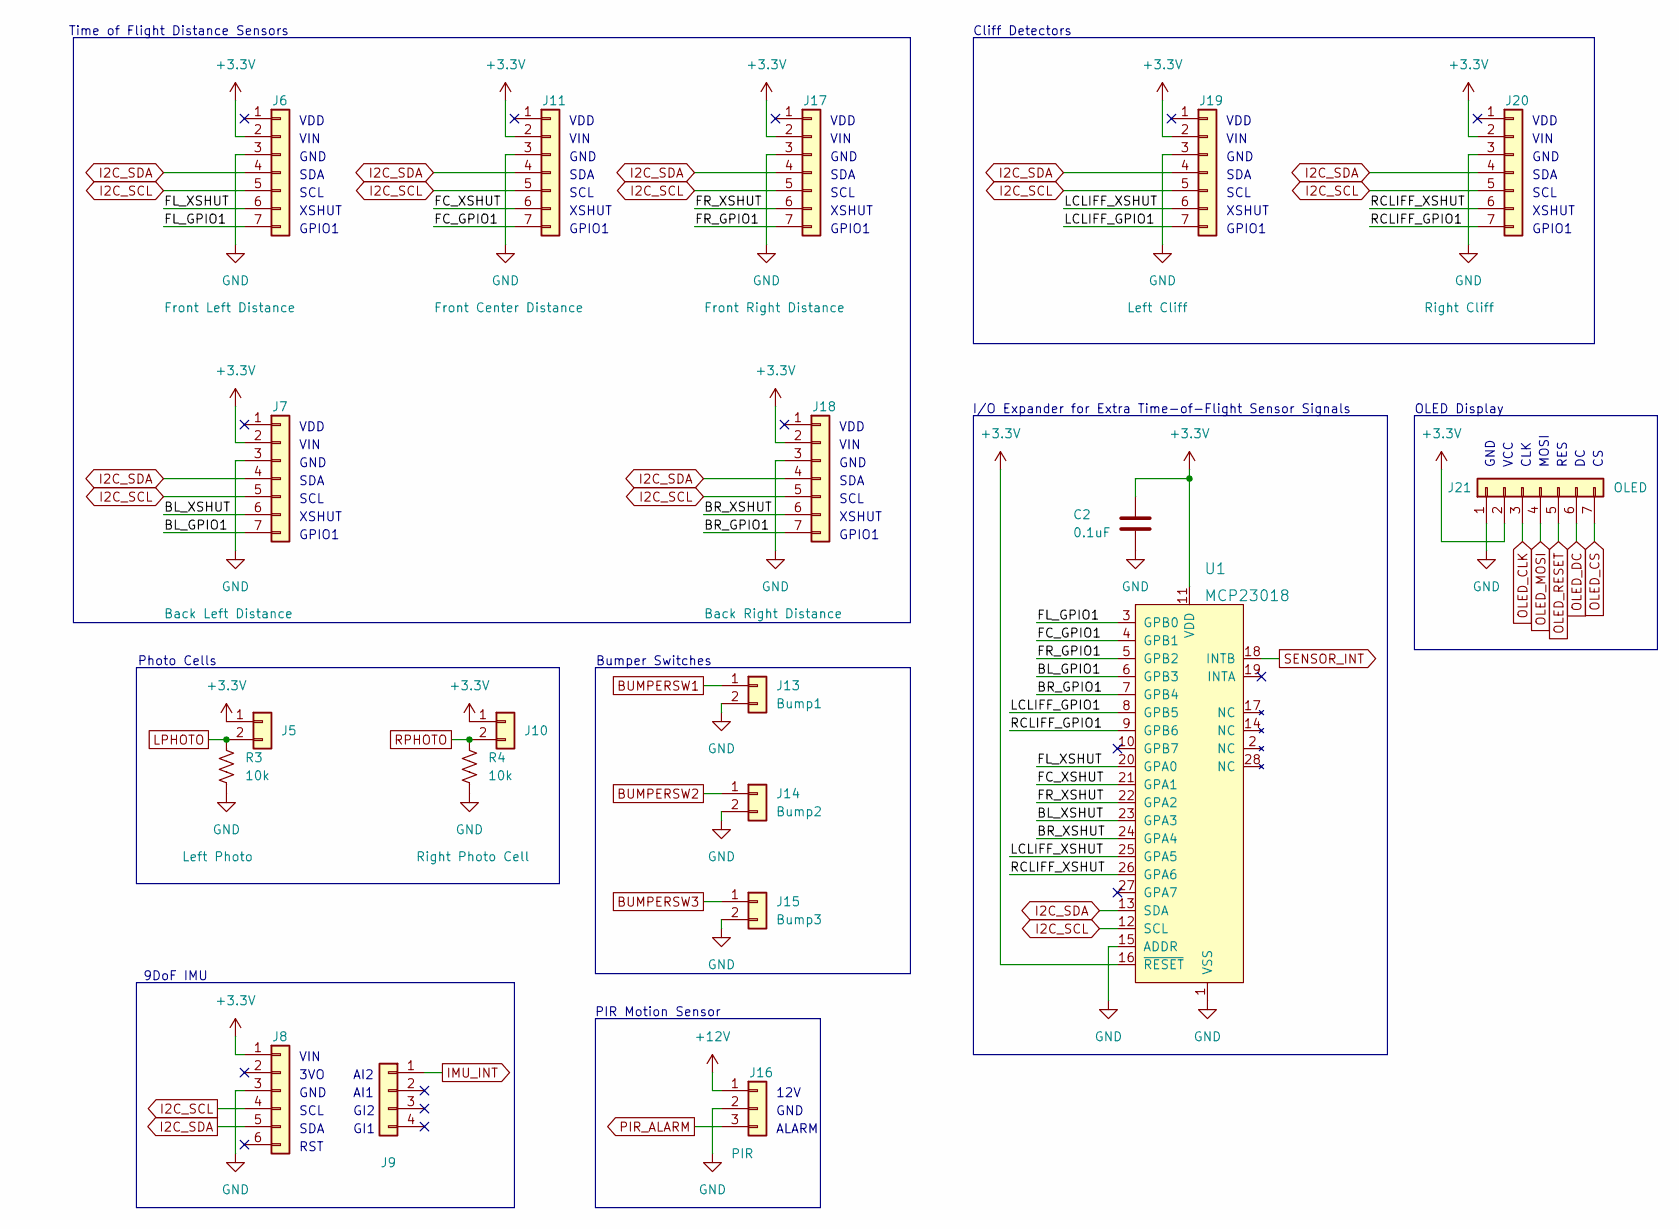
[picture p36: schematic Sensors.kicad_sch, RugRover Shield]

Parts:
C2: 0.1uF; C_0805_2012Metric_Pad1.18x1.45mm_HandSolder
J5: Left Photo; PinSocket_1x02_P2.54mm_Vertical
J6: Front Left Distance; PinSocket_1x07_P2.54mm_Vertical
J7: Back Left Distance; PinSocket_1x07_P2.54mm_Vertical
J8: IMU-1; PinSocket_1x06_P2.54mm_Vertical
J9: IMU-2; PinSocket_1x04_P2.54mm_Vertical
J10: Right Photo Cell; PinSocket_1x02_P2.54mm_Vertical
J11: Front Center Distance; PinSocket_1x07_P2.54mm_Vertical
J13: Bump1; PinSocket_1x02_P2.54mm_Horizontal
J14: Bump2; PinSocket_1x02_P2.54mm_Horizontal
J15: Bump3; PinSocket_1x02_P2.54mm_Horizontal
J16: PIR; PinSocket_1x03_P2.54mm_Vertical
J17: Front Right Distance; PinSocket_1x07_P2.54mm_Vertical
J18: Back Right Distance; PinSocket_1x07_P2.54mm_Vertical
J19: Left Cliff; PinSocket_1x07_P2.54mm_Horizontal
J20: Right Cliff; PinSocket_1x07_P2.54mm_Horizontal
J21: OLED; PinSocket_1x07_P2.54mm_Vertical
R3, R4: 10k; R_0805_2012Metric_Pad1.20x1.40mm_HandSolder
U1: MCP23018; SOIC-28W_7.5x17.9mm_P1.27mm; MPN MCP23018-E/SP; Digi-Key_PN MCP23018-E/SP-ND

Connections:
+3V3: C2.1, J5.1, J6.2, J7.2, J8.1, J10.1, J11.2, J17.2, J18.2, J19.2, J20.2, J21.2, U1.11 (VDD), U1.16 (~RESET); also elsewhere on the board
+12V: J16.1; also elsewhere on the board
/Sensors/BL_GPIO1: J7.7, U1.6 (GPB3)
/Sensors/BL_XSHUT: J7.6, U1.23 (GPA3)
/Sensors/BR_GPIO1: J18.7, U1.7 (GPB4)
/Sensors/BR_XSHUT: J18.6, U1.24 (GPA4)
/Sensors/FC_GPIO1: J11.7, U1.4 (GPB1)
/Sensors/FC_XSHUT: J11.6, U1.21 (GPA1)
/Sensors/FL_GPIO1: J6.7, U1.3 (GPB0)
/Sensors/FL_XSHUT: J6.6, U1.20 (GPA0)
/Sensors/FR_GPIO1: J17.7, U1.5 (GPB2)
/Sensors/FR_XSHUT: J17.6, U1.22 (GPA2)
/Sensors/LCLIFF_GPIO1: J19.7, U1.8 (GPB5)
/Sensors/LCLIFF_XSHUT: J19.6, U1.25 (GPA5)
/Sensors/RCLIFF_GPIO1: J20.7, U1.9 (GPB6)
/Sensors/RCLIFF_XSHUT: J20.6, U1.26 (GPA6)
BUMPERSW1: J13.1; also elsewhere on the board
BUMPERSW2: J14.1; also elsewhere on the board
BUMPERSW3: J15.1; also elsewhere on the board
GND: C2.2, J6.3, J7.3, J8.3, J11.3, J13.2, J14.2, J15.2, J16.2, J17.3, J18.3, J19.3, J20.3, J21.1, R3.2, R4.2, U1.1 (VSS), U1.15 (ADDR); also elsewhere on the board
I2C_SCL: J6.5, J7.5, J8.4, J11.5, J17.5, J18.5, J19.5, J20.5, U1.12 (SCL); also elsewhere on the board
I2C_SDA: J6.4, J7.4, J8.5, J11.4, J17.4, J18.4, J19.4, J20.4, U1.13 (SDA); also elsewhere on the board
IMU_INT: J9.1; also elsewhere on the board
LPHOTO: J5.2, R3.1; also elsewhere on the board
OLED_CLK: J21.3; also elsewhere on the board
OLED_CS: J21.7; also elsewhere on the board
OLED_DC: J21.6; also elsewhere on the board
OLED_MOSI: J21.4; also elsewhere on the board
OLED_RESET: J21.5; also elsewhere on the board
PIR_ALARM: J16.3; also elsewhere on the board
RPHOTO: J10.2, R4.1; also elsewhere on the board
SENSOR_INT: U1.18 (INTB); also elsewhere on the board

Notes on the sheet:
VIN
SDA
I/O Expander for Extra Time-of-Flight Sensor Signals
GND
GI1
XSHUT
GPIO1
RES
VDD
12V
CLK
SCL
Photo Cells
RST
Time of Flight Distance Sensors
AI1
OLED Display
GI2
PIR Motion Sensor
Bumper Switches
9DoF IMU
AI2
ALARM
3VO
Cliff Detectors
MOSI
VCC

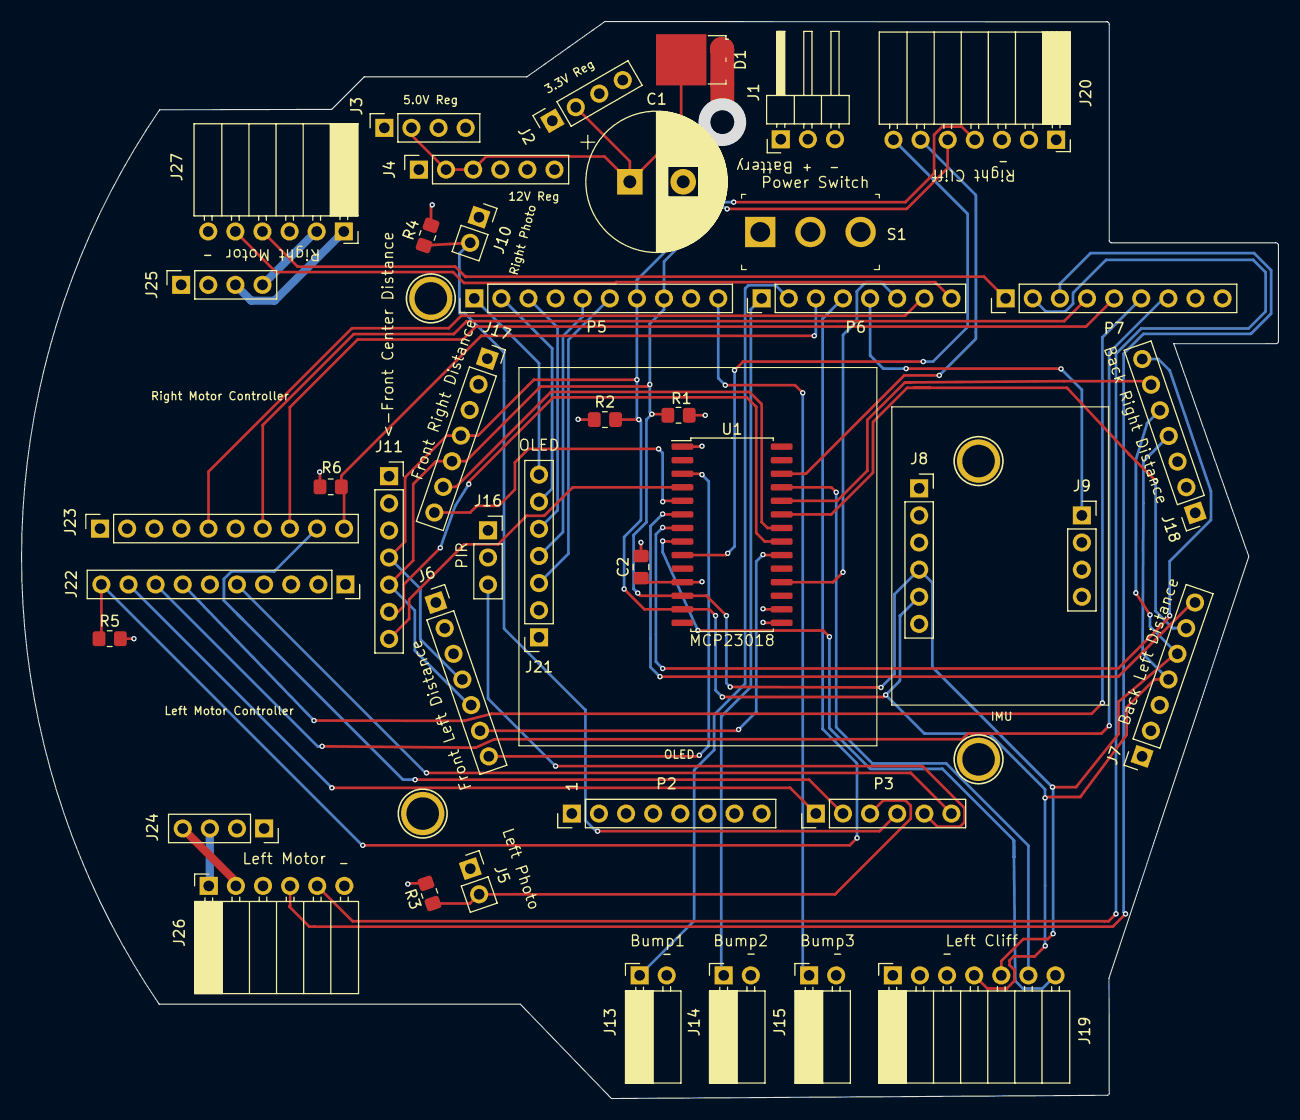
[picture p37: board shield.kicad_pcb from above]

Board: 4 copper layers, 117.7 x 100.9 mm, 46 parts (0 on the bottom side), 54 nets.

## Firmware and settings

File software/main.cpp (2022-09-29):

/*  Copyright (C) 2022  Adam Green (https://github.com/adamgreen)

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
    This program is distributed in the hope that it will be useful,
    but WITHOUT ANY WARRANTY; without even the implied warranty of
    MERCHANTABILITY or FITNESS FOR A PARTICULAR PURPOSE.  See the
    GNU General Public License for more details.
*/
/* Beginnings of firmware for RugRover robot.
   The hardware pin connections are:
   nRF52 Pin Number     Pin Name                Pin Description
          0.24          OLED_SCK_PIN            OLED Board - CLK
          0.25          OLED_MOSI_PIN           OLED Board - MOS
          0.26          OLED_DC_PIN             OLED Board - DC
          0.27          OLED_CS_PIN             OLED Board - CS
          0.2           OLED_RESET_PIN          OLED Board - RES
    ------------------------------------------------------------------------
          0.22          I2C_SCL_PIN             I2C Bus - SCL - Multiple Devices
          0.23          I2C_SDA_PIN             I2C Bus - SDA - Multiple Devices
    ------------------------------------------------------------------------
          0.14          IMU_INT_PIN             9DoF IMU - AINT2
    ------------------------------------------------------------------------
          0.8           LMOTOR_ENCODER_A_PIN    Left Motor Encoder A
          0.9           LMOTOR_ENCODER_B_PIN    Left Motor Encoder B
          0.10          RMOTOR_ENCODER_A_PIN    Right Motor Encoder A
          0.11          RMOTOR_ENCODER_B_PIN    Right Motor Encoder B
    ------------------------------------------------------------------------
          0.31          LMOTOR_EN_PIN           Left Motor Driver - EN
          0.21          LMOTOR_PWM1_PIN         Left Motor Driver - PWM1
          0.5           LMOTOR_PWM2_PIN         Left Motor Driver - PWM2
          0.15          LMOTOR_DIAG_PIN         Left Motor Driver - DIAG
          0.3           LMOTOR_OCM_PIN          Left Motor Driver - OCM
          0.12          RMOTOR_EN_PIN           Right Motor Driver - EN
          0.6           RMOTOR_PWM1_PIN         Right Motor Driver - PWM1
          0.7           RMOTOR_PWM2_PIN         Right Motor Driver - PWM2
          0.16          RMOTOR_DIAG_PIN         Right Motor Driver - DIAG
          0.4           RMOTOR_OCM_PIM          Right Motor Driver - OCM

*/
#include <ctype.h>
#include <stdio.h>
#include <math.h>
#include <app_util_platform.h>
#include <nrf_delay.h>
#include <nrf_gpio.h>
#include <core/mri.h>
#include <OLED_SH1106/OLED_SH1106.h>
#include <DifferentialDrive/DifferentialDrive.h>
#include <Navigate/Navigate.h>
#include <AdafruitPrecision9DoF/AdafruitPrecision9DoF.h>
#include <KalmanFilter/OrientationKalmanFilter.h>
#include <I2CAsync/I2CAsync.h>



// Parameters to turn on/off more expensive code that is mostly used for testing/debugging.
// Should the navigate code calculate statistics about the mean and variance of the system model. Useful for
// determining what the Q covariance matrix for the model should be.
#define DEBUG_CALCULATE_STATS_FOR_SYSTEM_MODEL  false


// Blink this LED (LED4 on nRF52-DK) to show progress.
#define BLINK_LED_PIN   20

// The SPIM peripheral instance to use for communicating with the OLED. Note that SPIM instances share the same
// resources as TWI (I2C).
#define OLED_SPI_INSTANCE   0

// Pins connected to the SPI signals used by the SH1106 OLED driver.
#define OLED_SCK_PIN    24
#define OLED_MOSI_PIN   25
#define OLED_CS_PIN     27
#define OLED_DC_PIN     26
#define OLED_RESET_PIN  2

// The I2C (TWI) peripheral instance to use for communicating with the IMU and time of flight range sensors.
// Can't be 0 as that instance is shared with the SPI peripheral used above for the OLED.
#define I2C_INSTANCE    1

// The frequency at which the I2C bus should be run. Using the fastest supported since I need to query so many sensors.
#define I2C_FREQUENCY   NRF_TWI_FREQ_400K

// The pins connected to the I2C (TWI) bus.
#define I2C_SCL_PIN     22
#define I2C_SDA_PIN     23

// The 9DoF IMU will issue an interrupt on the interrupt 2 pin of its accelerometer/magnetometer device when next
// sample is ready.
#define IMU_INT_PIN     14

// The sampling frequency at which the IMU should be run.
#define IMU_SAMPLE_RATE MOTOR_PID_FREQUENCY

// Pins connected to the motor quadrature encoders.
#define LMOTOR_ENCODER_A_PIN    8
#define LMOTOR_ENCODER_B_PIN    9
#define RMOTOR_ENCODER_A_PIN    10
#define RMOTOR_ENCODER_B_PIN    11

// Pins connected to the motor drivers.
#define LMOTOR_EN_PIN       31
#define LMOTOR_PWM1_PIN     21
#define LMOTOR_PWM2_PIN     5
#define LMOTOR_DIAG_PIN     15
#define LMOTOR_OCM_PIN      3
#define RMOTOR_EN_PIN       12
#define RMOTOR_PWM1_PIN     6
#define RMOTOR_PWM2_PIN     7
#define RMOTOR_DIAG_PIN     16
#define RMOTOR_OCM_PIN      4

// Should the motor's idea of forward be reversed?
#define LMOTOR_REVERSE      true
#define RMOTOR_REVERSE      false

// The number of encoder ticks per revolution of the wheel.
#define MOTOR_TICKS_PER_REV 1250

// The next 3 values are found through the calibration process and will be different for each bot and can even
// change over time.
// * The distance between the wheels in mm.
#define WHEELBASE           128.1868f
// * The diameter of the left wheel in mm.
#define LEFT_WHEEL_DIAMETER 80.65f
// * The diameter of the right wheel as a ratio of the left wheel (will be found during calibration).
#define RIGHT_WHEEL_RATIO   1.00f

// The calculated diameter of the right wheel based on left wheel and preceding ratio.
#define RIGHT_WHEEL_DIAMETER    (RIGHT_WHEEL_RATIO * LEFT_WHEEL_DIAMETER)

// The frequency to be used for the motor PWM signal.
#define MOTOR_PWM_FREQUENCY 20000

// Don't allow motor current to go over 1.5A.
#define MOTOR_MAX_CURRENT_mA    1500

/* PID constants used for the motors.
        ΔPV=15.500001
        ΔCO=30.000000
        Kp=0.516667
        Tp=60028 us
        ϴp=10004 us
        Aggressive Kc=9.678014
        Moderate Kc=1.480167
        Conservative Kc=0.156291
        Ti=0.065030 s
        Td=0.004617 s
*/
#define SPEED_PID_Kc            1.480167f
#define SPEED_PID_Ti            0.065030f
#define SPEED_PID_Td            0.004617f

/* Constants used for the navigation heading PI loop.
    slope1 = 3.014416
    slope2 = -3.071422
    CO1 = 0.250000
    CO2 = -0.250000
    Kp* = 12.171677
    Өp = 0.112236
    Tc = 0.336708
    Kc = 0.320254
    Ti = 0.785653
*/
#define HEADING_PID_Kc            0.320254f
#define HEADING_PID_Ti            0.785653f
#define HEADING_PID_Td            0.0f

/* Constants used for the navigation distance PI loop.
    slope1 = 113.845070
    slope2 = -117.282158
    CO1 = 0.250000
    CO2 = -0.250000
    Kp* = 462.254456
    Өp = 0.130037
    Tc = 0.390112
    Kc = 0.007278
    Ti = 0.910261
*/
#define DISTANCE_PID_Kc            0.007278f
#define DISTANCE_PID_Ti            0.910261f
#define DISTANCE_PID_Td            0.0f

// Thresholds used in the Navigate module to determine when close enough to a waypoint.
#define THRESHOLD_DISTANCE      0.5f
#define THRESHOLD_ANGLE         (0.5f * DEGREE_TO_RADIAN)

// The heading correction limits are based on the current forward speed. This macro specifies that ratio.
#define HEADING_VS_FORWARD_SPEED    0.5f

// When braking, wait for this many samples to return 0 encoder ticks before consider the stop to be complete.
#define BRAKE_ZERO_SAMPLE       5

// Number of IMU samples to run through the Kalman filter before start to allow it to stabilize.
#define IMU_STABILIZATION_SAMPLES   (5 * MOTOR_PID_FREQUENCY)

// PID Frequency in Hz.
#define MOTOR_PID_FREQUENCY     100

// Don't allow the PID controller to command the motor power past this percentage value (0 - 100).
#define MOTOR_PID_MAX_PERCENT   80


// Dimensions of the 1.3" OLED screen.
#define OLED_WIDTH      128
#define OLED_HEIGHT     64
// The Pololu's OLED screen's columns are centered on the 132 segment drivers.
#define OLED_COLUMN_OFFSET  ((OLED_SH1106_MAX_WIDTH-OLED_WIDTH)/2)
// The OLED screen's rows use up all of the 64 common drivers.
#define OLED_ROW_OFFSET     0



// Enumeration of routines which can be run from the main loop.
enum DebugRoutines
{
    DEBUG_NAVIGATE_WITH_ODOMETRY = 1,
    DEBUG_NAVIGATE_WITH_COMPASS = 2,
    DEBUG_NAVIGATE_WITH_ODOMETRY_GYRO_FUSION = 3,
    DEBUG_PID = 4,
    DEBUG_PID_SPEED_CALIBRATE = 5,
    DEBUG_PID_HEADING_CALIBRATE = 6,
    DEBUG_PID_DISTANCE_CALIBRATE = 7,
    DEBUG_IMU_RAW = 8,
    DEBUG_IMU_ORIENTATION = 9,
    DEBUG_MAX
};

// Enumeration of IMU dumping types.
enum DebugImuType
{
    IMU_RAW,
    IMU_ORIENTATION
};



// 9DoF IMU Configuration / Calibration settings
// I followed my older notes to obtain these calibration values:
//      https://github.com/adamgreen/Ferdinand14#august-19-2014
static SensorCalibration g_imuCalibration =
{
    // The initial P, Q and R covariance matrices for the Kalman filter are
    // initialized with these values on the diagonal.
    // P: The expected initial error in the model.
    // Q: The expected variance the gyro measurements will have on the model's
    //    quaternion during each iteration of the filter.
    // R: The expected variance the accelerometer and magnetometer measurements
    //    will have on the representative quaternion during each iteration of the
    //    filter.
    .initialVariance = 2.0E-4f,
    .gyroVariance = 3.5E-10f,
    .accelMagVariance = 2.0E-4f,

    // These gyro coefficients provide the linear equation (y=ax + b) which relates
    // sensor temperature to its bias (drift).
    .gyroCoefficientA = {  0.8812f,  2.1546f, 0.8783f },
    .gyroCoefficientB = { -16.804f, -9.2753f, 19.812f },

    // These scale indicates LSBs (least significant bits) per degree/sec.  They
    // should be close to the 128 LSB/dsp value from the FXAS21002C specification.
    .gyroScale = { 128.0f, 128.0f, 128.0f },

    // This vector specifies the declination correction to be applied to
    // convert magnetic north to true north.
    // It can be calculated here: http://www.ngdc.noaa.gov/geomag-web/#declination
    // The 3 element vector represents: degrees,minutes,seconds
    .declinationCorrection = { 15.0f, 54.0f, 0.0f },

    // Correct for how device is mounted on robot.
    // The 3 element vector represents: degrees,minutes,seconds
    .mountingCorrection = { 90.0f, 0.0f, 0.0f },

    // These min/max configuration values were found by rotating my sensor setup
    // and noting min/max values seen in calibration sketch.
    .accelMin = { -4008, -4140, -3900 },
    .accelMax = { 4320, 3790, 4204 },
    .magMin = { -575, -670, -865 },
    .magMax = { 333, 288, 100 },

    // Control the swizzle for each sensor (ie. map the x, y, z axis for each sensor
    // to the x, y, z axis of the coordinate system we want to use for the output).
    // For example: 3,-2,1 indicates that final x should be taken from the sensor's
    //              z axis, the final y should be taken from the sensor's y axis but
    //              after inverting its value, and the final z should be taken from
    //              the sensor's x axis.
    // The axis are swizzled to match a right hand axis version of that used by
    // Processing: X points right  Y points down  Z points into the screen
    // This accounts for the fact that a robot might want to assume an x axis that
    // is a different axis for the sensor itself and it also accounts for the
    // scenario where each sensor (accelerometer, magnetometer, and gyro) has their
    // axis aligned differently.
    .accelSwizzle = { 1, -3, 2 },
    .magSwizzle = { 1, -3, 2 },
    .gyroSwizzle = { 1, -3, 2 }
};

// The likely odometry angle delta error is due to 1 encoder tick's impact on the robot's heading.
// Specified in radians.
#define ODOMETRY_ERROR      ((1.0f/MOTOR_TICKS_PER_REV)*(float)M_PI*LEFT_WHEEL_DIAMETER/WHEELBASE)

// Gyro error is specified in gyro's data sheet. Specified in radians/second.
// The data sheet indicates that it should be ~2x this but this is what I saw during the calibration run.
#define GYRO_ERROR          (18.158f/128.0f)

#define ODOMETRY_VARIANCE   (ODOMETRY_ERROR*ODOMETRY_ERROR)
#define GYRO_VARIANCE       (GYRO_ERROR*GYRO_ERROR)

// Calibration values for the heading kalman filter which combines wheel odometry measurement of heading angle change
// with yaw gyro rate measurements.
HeadingCalibration g_headingCalibration =
{
    // There are 128 least significant bits per degree according to gyro's data sheet.
    .gyroScale = 128.0f,
    // The robot isn't moving when navigation starts at angle 0.0 so the first 2 parameters are known 100%. The
    // gyro drift will be estimated as the current gyro rate when no movement is being made. This should be within
    // the gyro's noise spec.
    .initialModelVariances = {0.0f, 0.0f, GYRO_VARIANCE},
    // Found by running model with odometry alone in testNavigateRoutine() and keeping stats on how much each actual
    // sample differs from the estimate.
    .modelVariances = {0.000003f, 0.025384, 0.0f},
    // The odometry error is calculated above and the gyro error comes from data sheet.
    .sensorVariances = {ODOMETRY_VARIANCE, GYRO_VARIANCE}
};

// SPIM instance used for driving the OLED.
static const nrf_drv_spi_t  g_spiOLED = NRF_DRV_SPI_INSTANCE(OLED_SPI_INSTANCE);

// OLED Screen.
static OLED_SH1106          g_OLED(OLED_WIDTH, OLED_HEIGHT, OLED_COLUMN_OFFSET, OLED_ROW_OFFSET,
                                   &g_spiOLED, OLED_SCK_PIN, OLED_MOSI_PIN, OLED_DC_PIN);

// TWIM (I2C Master) instance used for driving IMU and time of flight sensors.
static const nrf_drv_twi_t  g_i2c = NRF_DRV_TWI_INSTANCE(I2C_INSTANCE);

// Wrapper around TWIM (I2C master) instance which adds a circular queue to manage multiple async transfers.
static I2CAsync             g_i2cAsync(&g_i2c, I2C_SCL_PIN, I2C_SDA_PIN, I2C_FREQUENCY, _PRIO_APP_MID);

// Adafruit's 9DoF IMU.
static AdafruitPrecision9DoF g_imu(&g_i2cAsync, IMU_INT_PIN, IMU_SAMPLE_RATE);

// Kalman filter used to determine 3D orientation.
static OrientationKalmanFilter g_orientation(IMU_SAMPLE_RATE, &g_imuCalibration);

// Analog to digital converter object.
static SAADCScanner         g_adc(NRF_SAADC_RESOLUTION_12BIT, false, _PRIO_APP_LOWEST);

// PWM peripheral instance used for the motor drivers.
static nrf_drv_pwm_t        g_PWM = NRF_DRV_PWM_INSTANCE(0);
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
int main(void)
{
    verifyUICRBits();

    initDataFile();

    initOLED();
    initI2C();

    // The software quadrature decoder and IMU uses GPIOTE so initialize it now.
    initGPIOTE_AtHighestAppPriority();

    // Get the IMU sensor up and running.
    bool result = g_imu.init();
    ASSERT ( result );

    // Initialize the ADC object which scans all of the configured ADC channels as often as possible (~200kHz).
    result = g_adc.init();
    ASSERT ( result );

    // Initialize the closed loop different drive system.
    result = g_drive.init();
    ASSERT ( result );
    g_drive.enable();

    // Initialize GPIO pin for LED that is flashed to show progress.
    nrf_gpio_cfg_output(BLINK_LED_PIN);

    // Far enough along that it is safe for MRI to call our hooks to disable motors when entering the debugger.
    mriSetDebuggerHooks(enteringDebuggerHook, leavingDebuggerHook, NULL);

    while (true)
    {
        g_dbg = 0;
        switch (g_dbgRoutine)
        {
            case DEBUG_NAVIGATE_WITH_ODOMETRY:
                testNavigateRoutine(Navigate::ODOMETRY_ONLY);
                break;
            case DEBUG_NAVIGATE_WITH_COMPASS:
                testNavigateRoutine(Navigate::COMPASS_ONLY);
                break;
            case DEBUG_NAVIGATE_WITH_ODOMETRY_GYRO_FUSION:
                testNavigateRoutine(Navigate::ODOMETRY_GYRO_FUSION);
                break;
            case DEBUG_PID:
                testPidRoutine();
                break;
            case DEBUG_PID_SPEED_CALIBRATE:
                testPidSpeedCalibrateRoutine();
                break;
            case DEBUG_PID_HEADING_CALIBRATE:
                testPidHeadingCalibrateRoutine();
                break;
            case DEBUG_PID_DISTANCE_CALIBRATE:
                testPidDistanceCalibrateRoutine();
                break;
            case DEBUG_IMU_RAW:
                debugImuRoutine(IMU_RAW);
                break;
            case DEBUG_IMU_ORIENTATION:
                debugImuRoutine(IMU_ORIENTATION);
                break;
            default:
                break;
        }

        g_dbgRoutine = (DebugRoutines)displayDebugMenuAndGetOption(
                                        "1. Test Navigate with Odometry\n"
                                        "2. Test Navigate with Compass\n"
                                        "3. Test Navigate with Odometry/Gyro Fusion\n"
                                        "4. Test PID\n"
                                        "5. Run Speed PID calibration\n"
                                        "6. Run Heading PID calibration\n"
                                        "7. Run Distance PID calibration\n"
                                        "8. Test IMU Raw\n"
                                        "9. Test IMU Orientation\n", DEBUG_MAX);
    }
}

static void initDataFile()
{
    // Open the special file to which data can be sent wirelessly to application running on mac.
    g_pDataFile = fdopen(0x7FFF, "w");
    // UNDONE: May not want this to be line buffered in the future.
    setvbuf(g_pDataFile, NULL, _IOLBF, 0);
}

static void initOLED()
{
    testHardWiringSomeOLEDPins();

    g_OLED.init();
    g_OLED.setRotation(2);
    g_OLED.setBrightness(16);
    g_OLED.setTextColor(1, 0);
}

static void testHardWiringSomeOLEDPins()
{
    // Looks like I can just hard wire CS low and RESET high on the OLED. This will free up 2 pins.
    nrf_gpio_pin_clear(OLED_CS_PIN);
    nrf_gpio_cfg_output(OLED_CS_PIN);
    nrf_gpio_pin_set(OLED_RESET_PIN);
    nrf_gpio_cfg_output(OLED_RESET_PIN);
}

static void initI2C()
{
    bool result = g_i2cAsync.init();
    ASSERT ( result );

    configureI2CPinsToDisablePullUpAndUseHigherCurrentSinkTo0V();

    g_i2cAsync.enable();
}

static void configureI2CPinsToDisablePullUpAndUseHigherCurrentSinkTo0V()
{
    // Use strong sink to 0 and disable internal pull-up as we have external ones.
    // Should be done after I2C is init since it will configure the pins and before the I2C peripheral is actually
    // enabled.
    nrf_gpio_cfg(I2C_SCL_PIN, NRF_GPIO_PIN_DIR_INPUT, NRF_GPIO_PIN_INPUT_CONNECT, NRF_GPIO_PIN_NOPULL,
                 NRF_GPIO_PIN_H0D1, NRF_GPIO_PIN_NOSENSE);
    nrf_gpio_cfg(I2C_SDA_PIN, NRF_GPIO_PIN_DIR_INPUT, NRF_GPIO_PIN_INPUT_CONNECT, NRF_GPIO_PIN_NOPULL,
                 NRF_GPIO_PIN_H0D1, NRF_GPIO_PIN_NOSENSE);
}

static void initGPIOTE_AtHighestAppPriority()
{
    nrf_drv_gpiote_init();
    NVIC_SetPriority(GPIOTE_IRQn, _PRIO_APP_HIGH);
}

static uint32_t displayDebugMenuAndGetOption(const char* pOptionsString, uint32_t maxOption)
{
    g_OLED.clearScreen();
    g_OLED.printf("Debug Menu in GDB");
    g_OLED.refreshAndBlock();
    while (true)
    {
        uint32_t choice = 0;
        char     buffer[16];

        printf("\n\nDebug Menu\n");
        printf("%s", pOptionsString);
        printf("\nSelect: ");
        fgets(buffer, sizeof(buffer), stdin);
        choice = strtoul(buffer, NULL, 10);
        if (choice < 1 || choice >= maxOption)
        {
            printf("Invalid selection\n");
        }
        else
        {
            return choice;
        }
    }
}

static void testNavigateRoutine(Navigate::HeadingSource headingSource)
{
    DriveValues zeroPower{0, 0};
    const float driveSpeed_mps = 0.25f;
    const float turnSpeed_mps = 0.25f;
    const float angleThreshold = 15.0f * DEGREE_TO_RADIAN;
    float leftWheelDiameter = LEFT_WHEEL_DIAMETER;
    float rightWheelDiameter = RIGHT_WHEEL_DIAMETER;
    float wheelRatio = rightWheelDiameter / leftWheelDiameter;
    float wheelbase = WHEELBASE;
    HeadingKalmanFilter headingFilter(&g_headingCalibration);

    uint32_t logBuffer[2048/sizeof(uint32_t)];
    g_navigate.setLogBuffer(logBuffer, sizeof(logBuffer));
    while (true)
    {
        printf("\n\n"
               "Update odometry settings.\n"
               "Just press <Return> to keep current setting.\n");

        leftWheelDiameter = getFloatOption("Left Wheel Diameter in mm", leftWheelDiameter);
        wheelRatio = getFloatOption("Right Wheel Diameter / Left Wheel Diameter ratio", wheelRatio);
        rightWheelDiameter = leftWheelDiameter * wheelRatio;
        wheelbase = getFloatOption("Wheel base in mm", wheelbase);

        char input[8];
        enum { NEITHER, STRAIGHT, TURN, CLOCKWISE, COUNTERCLOCKWISE } testMode = NEITHER;
        do
        {
            printf("\nDrive (s)traight, (t)urn in place, (c)lockwise, (x)counter-clockwise: ");
            fgets(input, sizeof(input), stdin);
            switch (tolower(input[0]))
            {
                case 's':
                    testMode = STRAIGHT;
                    break;
                case 't':
                    testMode = TURN;
                    break;
                case 'c':
                    testMode = CLOCKWISE;
                    break;
                case 'x':
                    testMode = COUNTERCLOCKWISE;
                    break;
                default:
                    break;
            }
        } while (testMode == NEITHER);

        // Enter main action loop.
        uint32_t count = 0;

        // Setup the fixed heading text on the OLED.
        g_OLED.clearScreen();
        g_OLED.printf("  Pos X:\n");
        g_OLED.printf("  Pos Y:\n");
        g_OLED.printf("Heading:\n");
        g_OLED.printf("Compass:\n");
        g_OLED.printf("  Ticks:\n");
        g_OLED.printf(" Max mA:\n");

        g_navigate.reset();
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

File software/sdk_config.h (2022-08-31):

#ifndef SDK_CONFIG_H
#define SDK_CONFIG_H
// <<< Use Configuration Wizard in Context Menu >>>\n
#ifdef USE_APP_CONFIG
#include "app_config.h"
#endif
// <h> nRF_BLE

//==========================================================
// <q> BLE_ADVERTISING_ENABLED  - ble_advertising - Advertising module


#ifndef BLE_ADVERTISING_ENABLED
#define BLE_ADVERTISING_ENABLED 0
#endif

// <q> BLE_DTM_ENABLED  - ble_dtm - Module for testing RF/PHY using DTM commands


#ifndef BLE_DTM_ENABLED
#define BLE_DTM_ENABLED 0
#endif

// <q> BLE_RACP_ENABLED  - ble_racp - Record Access Control Point library


#ifndef BLE_RACP_ENABLED
#define BLE_RACP_ENABLED 0
#endif

// <q> NRF_BLE_QWR_ENABLED  - nrf_ble_qwr - Queued writes support module (prepare/execute write)


#ifndef NRF_BLE_QWR_ENABLED
#define NRF_BLE_QWR_ENABLED 0
#endif

// <q> PEER_MANAGER_ENABLED  - peer_manager - Peer Manager


#ifndef PEER_MANAGER_ENABLED
#define PEER_MANAGER_ENABLED 0
#endif

// </h>
//==========================================================

// <h> nRF_BLE_Services

//==========================================================
// <q> BLE_ANCS_C_ENABLED  - ble_ancs_c - Apple Notification Service Client


#ifndef BLE_ANCS_C_ENABLED
#define BLE_ANCS_C_ENABLED 0
#endif

// <q> BLE_ANS_C_ENABLED  - ble_ans_c - Alert Notification Service Client


#ifndef BLE_ANS_C_ENABLED
#define BLE_ANS_C_ENABLED 0
#endif

// <q> BLE_BAS_C_ENABLED  - ble_bas_c - Battery Service Client


#ifndef BLE_BAS_C_ENABLED
#define BLE_BAS_C_ENABLED 0
#endif

// <q> BLE_BAS_ENABLED  - ble_bas - Battery Service


#ifndef BLE_BAS_ENABLED
#define BLE_BAS_ENABLED 0
#endif

// <q> BLE_CSCS_ENABLED  - ble_cscs - Cycling Speed and Cadence Service


#ifndef BLE_CSCS_ENABLED
#define BLE_CSCS_ENABLED 0
#endif

// <q> BLE_CTS_C_ENABLED  - ble_cts_c - Current Time Service Client


#ifndef BLE_CTS_C_ENABLED
#define BLE_CTS_C_ENABLED 0
#endif

// <q> BLE_DIS_ENABLED  - ble_dis - Device Information Service


#ifndef BLE_DIS_ENABLED
#define BLE_DIS_ENABLED 0
#endif

// <q> BLE_GLS_ENABLED  - ble_gls - Glucose Service


#ifndef BLE_GLS_ENABLED
#define BLE_GLS_ENABLED 0
#endif

// <q> BLE_HIDS_ENABLED  - ble_hids - Human Interface Device Service


#ifndef BLE_HIDS_ENABLED
#define BLE_HIDS_ENABLED 0
#endif

// <e> BLE_HRS_C_ENABLED - ble_hrs_c - Heart Rate Service Client
//==========================================================
#ifndef BLE_HRS_C_ENABLED
#define BLE_HRS_C_ENABLED 0
#endif
#if  BLE_HRS_C_ENABLED
// <o> BLE_HRS_C_RR_INTERVALS_MAX_CNT - Maximum number of RR_INTERVALS per notification to be decoded
#ifndef BLE_HRS_C_RR_INTERVALS_MAX_CNT
#define BLE_HRS_C_RR_INTERVALS_MAX_CNT 30
#endif

#endif //BLE_HRS_C_ENABLED
// </e>

// <q> BLE_HRS_ENABLED  - ble_hrs - Heart Rate Service


#ifndef BLE_HRS_ENABLED
#define BLE_HRS_ENABLED 0
#endif

// <q> BLE_HTS_ENABLED  - ble_hts - Health Thermometer Service


#ifndef BLE_HTS_ENABLED
#define BLE_HTS_ENABLED 0
#endif

// <q> BLE_IAS_C_ENABLED  - ble_ias_c - Immediate Alert Service Client


#ifndef BLE_IAS_C_ENABLED
#define BLE_IAS_C_ENABLED 0
#endif

// <q> BLE_IAS_ENABLED  - ble_ias - Immediate Alert Service


#ifndef BLE_IAS_ENABLED
#define BLE_IAS_ENABLED 0
#endif

// <q> BLE_LBS_C_ENABLED  - ble_lbs_c - Nordic LED Button Service Client


#ifndef BLE_LBS_C_ENABLED
#define BLE_LBS_C_ENABLED 0
#endif

// <q> BLE_LBS_ENABLED  - ble_lbs - LED Button Service


#ifndef BLE_LBS_ENABLED
#define BLE_LBS_ENABLED 0
#endif

// <q> BLE_LLS_ENABLED  - ble_lls - Link Loss Service


#ifndef BLE_LLS_ENABLED
#define BLE_LLS_ENABLED 0
#endif

// <q> BLE_NUS_C_ENABLED  - ble_nus_c - Nordic UART Central Service


#ifndef BLE_NUS_C_ENABLED
#define BLE_NUS_C_ENABLED 0
#endif

// <q> BLE_NUS_ENABLED  - ble_nus - Nordic UART Service


#ifndef BLE_NUS_ENABLED
#define BLE_NUS_ENABLED 1
#endif

// <q> BLE_RSCS_C_ENABLED  - ble_rscs_c - Running Speed and Cadence Client


#ifndef BLE_RSCS_C_ENABLED
#define BLE_RSCS_C_ENABLED 0
#endif

// <q> BLE_RSCS_ENABLED  - ble_rscs - Running Speed and Cadence Service


#ifndef BLE_RSCS_ENABLED
#define BLE_RSCS_ENABLED 0
#endif

// <q> BLE_TPS_ENABLED  - ble_tps - TX Power Service


#ifndef BLE_TPS_ENABLED
#define BLE_TPS_ENABLED 0
#endif

// </h>
//==========================================================

// <h> nRF_Drivers

//==========================================================
// <e> ADC_ENABLED - nrf_drv_adc - Driver for ADC peripheral (nRF51)
//==========================================================
#ifndef ADC_ENABLED
#define ADC_ENABLED 0
#endif
#if  ADC_ENABLED
// <o> ADC_CONFIG_IRQ_PRIORITY  - Interrupt priority


// <i> Priorities 0,2 (nRF51) and 0,1,4,5 (nRF52) are reserved for SoftDevice
// <0=> 0 (highest)
// <1=> 1
// <2=> 2
// <3=> 3
// <4=> 4
// <5=> 5
// <6=> 6
// <7=> 7

#ifndef ADC_CONFIG_IRQ_PRIORITY
#define ADC_CONFIG_IRQ_PRIORITY 7
#endif
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

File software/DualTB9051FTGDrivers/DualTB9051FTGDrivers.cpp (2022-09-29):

/*  Copyright (C) 2022  Adam Green (https://github.com/adamgreen)

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
    This program is distributed in the hope that it will be useful,
    but WITHOUT ANY WARRANTY; without even the implied warranty of
    MERCHANTABILITY or FITNESS FOR A PARTICULAR PURPOSE.  See the
    GNU General Public License for more details.
*/
#include <string.h>
#include <app_util_platform.h>
#include <nrf_gpio.h>
#include "DualTB9051FTGDrivers.h"


// Macros to convert between ADC readings and mA current values for the motor driver.
// Input analog range of (0-4095) to (0-3.3V)
#define ADC_TO_V(X) ((X)*33/40950)
// Input voltage range of (0-3.3V) to mA
//      I = OCMV / 220ohm * 1/0.00223
#define V_TO_mA(X) ((X)*2038)
// Input analog range of (0-4095) to mA
#define ADC_TO_mA(X) (((int32_t)X)*67254/40950)
// Input motor current in mA to ADC range of (0-4095)
#define mA_TO_ADC(X) ((X)*40950/67254)



DualTB9051FTGDrivers* DualTB9051FTGDrivers::m_pThis = NULL;



DualTB9051FTGDrivers::DualTB9051FTGDrivers(uint8_t leftEnablePin, uint8_t leftPwm1Pin, uint8_t leftPwm2Pin,
                                           uint8_t leftDiagPin, uint8_t leftOcmPin, bool leftInvert,
                                           uint8_t rightEnablePin, uint8_t rightPwm1Pin, uint8_t rightPwm2Pin,
                                           uint8_t rightDiagPin, uint8_t rightOcmPin, bool rightInvert,
                                           SAADCScanner* pADC,
                                           nrf_drv_pwm_t* pPWM, uint32_t frequency,
                                           uint32_t maxCurrent_mA, uint8_t irqPriority /* = _PRIO_APP_LOWEST */)
: m_leftMotor(this, leftEnablePin, leftDiagPin, leftOcmPin, maxCurrent_mA, leftInvert),
  m_rightMotor(this, rightEnablePin, rightDiagPin, rightOcmPin, maxCurrent_mA, rightInvert)
{
    // Only support one instance of this class.
    ASSERT ( m_pThis == NULL );
    m_pThis = this;

    // Must provided pointer to PWM object used with the motor drivers.
    ASSERT ( pPWM );

    // PWM frequency for these motor drivers can't exceed 20kHz.
    ASSERT ( frequency > 0 && frequency <= 20000 );

    m_pADC = pADC;
    m_pPWM = pPWM;
    m_leftPwm1Pin = leftPwm1Pin;
    m_leftPwm2Pin = leftPwm2Pin;
    m_rightPwm1Pin = rightPwm1Pin;
    m_rightPwm2Pin = rightPwm2Pin;
    m_frequency = frequency;
    m_counterTop = 0;
    memset(&m_dutyCycles, 0, sizeof(m_dutyCycles));
    m_irqPriority = irqPriority;
}

bool DualTB9051FTGDrivers::init()
{
    bool validFreq = false;
    nrf_pwm_clk_t baseClock = NRF_PWM_CLK_125kHz;
    uint16_t counterTop = 3;
    for (uint32_t div = 0, freq=16000000 ; freq >= 125000 ; freq /= 2, div++)
    {
        uint32_t top = freq/m_frequency;
        if (top <= 0x7FFF)
        {
            baseClock = (nrf_pwm_clk_t)div;
            counterTop = (uint16_t)top;
            validFreq = true;
            break;
        }
    }
    if (!validFreq)
    {
        return false;
    }

    nrf_drv_pwm_config_t config =
    {
        .output_pins = {m_leftPwm1Pin, m_leftPwm2Pin, m_rightPwm1Pin, m_rightPwm2Pin},
        .irq_priority = m_irqPriority,
        .base_clock = baseClock,
        .count_mode = NRF_PWM_MODE_UP,
        .top_value = counterTop,
        .load_mode = NRF_PWM_LOAD_INDIVIDUAL,
        .step_mode = NRF_PWM_STEP_AUTO
    };
    ret_code_t result = nrf_drv_pwm_init(m_pPWM, &config, staticEventHandler);
    if (result != NRF_SUCCESS)
    {
        return false;
    }
    m_counterTop = counterTop;

    MotorDriver::DutyCycleSequences leftDutyCycles =
    { .dutyCyclePointers =
        {{.pPwm1 = &m_dutyCycles[0].channel_0,
          .pPwm2 = &m_dutyCycles[0].channel_1},
         {.pPwm1 = &m_dutyCycles[1].channel_0,
          .pPwm2 = &m_dutyCycles[1].channel_1}}
    };
    MotorDriver::DutyCycleSequences rightDutyCycles =
    { .dutyCyclePointers =
        {{.pPwm1 = &m_dutyCycles[0].channel_2,
          .pPwm2 = &m_dutyCycles[0].channel_3},
         {.pPwm1 = &m_dutyCycles[1].channel_2,
          .pPwm2 = &m_dutyCycles[1].channel_3}}
    };
    m_leftMotor.init(&leftDutyCycles, m_counterTop);
    m_rightMotor.init(&rightDutyCycles, m_counterTop);

    bool adcResult = m_leftMotor.initAdcToMeasureMotorCurrents(m_pADC);
    if (!adcResult)
    {
        return false;
    }
    adcResult = m_rightMotor.initAdcToMeasureMotorCurrents(m_pADC);
    if (!adcResult)
    {
        return false;
    }
    m_pADC->startScanning();

    nrf_pwm_sequence_t pwmSequence0 =
    {
        .values = { .p_individual = &m_dutyCycles[0] },
        .length = NRF_PWM_VALUES_LENGTH(m_dutyCycles[0]),
        .repeats = 0,
        .end_delay = 0
    };
    nrf_pwm_sequence_t pwmSequence1 =
    {
        .values = { .p_individual = &m_dutyCycles[1] },
        .length = NRF_PWM_VALUES_LENGTH(m_dutyCycles[1]),
        .repeats = 0,
        .end_delay = 0
    };
    uint32_t playbackFlags = NRF_DRV_PWM_FLAG_LOOP | NRF_DRV_PWM_FLAG_SIGNAL_END_SEQ0 | NRF_DRV_PWM_FLAG_SIGNAL_END_SEQ1;
    nrf_drv_pwm_complex_playback(m_pPWM, &pwmSequence0, &pwmSequence1, 1, playbackFlags);

    return true;
}
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

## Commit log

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2022-04-05 Cleanup PCB layout
    * Made the board outline a bit smaller.
    * Added the 3D .step files for all of the parts that I could find. This
    was all the parts except for the IMU from Adafruit.
    * Fixed an issue where I had the back distance sensors facing in the
    wrong direction.
    * Added CC BY-SA licensing info for the KiCad design files.
    [100SPxT1B4M2xE.stp, Motors.kicad_sch, PowerSupply.kicad_sch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]
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2022-04-19 Update CAD design for Chassis
    * Increased thickness from 2.5mm to 5.0mm to increase rigidity of the
    base.
    * Decreased height of standoffs mounting the nRF52 development kit to
    the chassis as the shorter standoffs work better.
    * Updated chassis photos after applying above design changes.
    [Chassis.3mf, Chassis.scad, Chassis.stl]
2022-04-19 Adding FlexTest files
    These files are for rectangular test patterns that I printed at various
    thickness and infill settings to determine their impact on stiffness.
    Test results were:
    * 5.0mm was much stiffer than 2.5mm.
    * 60% versus 30% infill didn't seem to have much impact on stiffness
    but the 60% infill did result in better elasticity as the 30% samples
    didn't always return to their original flat shape after I performed
    my test bends.
    [FlexTest.3mf, FlexTest.scad, FlexTest.stl]
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2022-04-30 Initial mriblue commit
    mriblue allows GDB to debug firmware on a nRF52 device using BLE as
    the communication mechanism. It uses my MRI debug monitor on the nRF52
    running at IRQ level 6. This allows it to:
    * Debug code that is running at IRQ level 7 or in the main thread.
    * Use the BLE stack configured to run at IRQ level 5 or higher as the
    communication channel.
    GDB can't communicate over BLE directly so there is also a command line
    application that runs on macos to bridge between BLE and TCP/IP. This
    code is found in the /mriblue/ folder.
    The code in this commit is mostly just a proof of concept and doesn't
    support everything need for debugging. I know it is missing:
    * CTRL+C support wh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
    [main.c, sdk_config.h]
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2022-04-30 Catch faults in mriblue
    This commit includes assembly language fault handlers that will pass in
    PSP, MSP, and EXC_RETURN to the C function mriFaultHandler(). This C
    function looks up the IRQ of the code which caused the fault and if its
    priority is low enough, a DebugMon interrupt can be pended before
    returning and allowing the NVIC to unwrap and execute DebugMon at
    priority level 6. Can't run MRI code straight from the fault handlers
    like usual since this would stop the BLE stack from running.
    If you crash in the BLE stack, mriFaultHandler() currently just hangs
    so that it could be debugged via Jlink. I will try to come up with a
    better solution in the future.
    [main.c]
2022-05-01 Fault handling fixes in mriblue
    * mriFaultHandler() now checks to see if the fault was actually caused
    by MRI when GDB requests accesses to invalid memory locations. This
    code was copied from the existing ThreadDebug library. Before this
    fix, such invalid accesses would cause mriFaultHandler() to enter its
    infinite loop.
    * getInterruptPriority() now shifts off the unused least significant
    bit of the interrupt priorities stored in the NVIC->IP registers.
    Before this fix faults in high priority interrupt handlers would be
    incorrectly detected as low priority and DebugMon pended.
    Other updates in this commit include:
    * "monitor reset" wasn't working because
    mriPlatform_CommHasT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
    [main.c]
2022-05-02 Firmware cleanup
    As I was investigating what I needed to do to make the current MRI
    over BLE proof of concept a bootloader, I noticed a few issues from
    the disassembly/map files:
    * My naming of the MemManage_Handler handler wasn't consistent with
    the name used by Nordic in their code so it was pulling in their
    default infinite looping version and not mine.
    * I can disable the GPIOTE module now as I am not using it anymore. I
    noticed that the GPIOTE interrupt vector was active when I didn't
    expect it to be.
    [sdk_config.h]
2022-05-03 Start of MRI based bootloader
    The mriblue_boot/ folder contains the MRI based bootloader that loads
    into FLASH just above the SoftDevice, where the application would
    normally reside. On startup, it initializes the BLE stack, the MRI
    core, and then reads the application's ISR vector table so that it can
    determine the location of its Reset_Handler. It will ask MRI to stop
    at the application's Reset_Handler routine, just before jumping to it.
    The developer is then free to set whatever breakpoint they want, before
    main() even starts running.
    I modified the firmware in the software/ folder to just blink 2 of the
    LEDs on the devkit and removed all of the BLE and MRI code. This will
    be the startin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
    [main.c, sdk_config.h]
2022-05-04 Start of load/flash support
    Can now issue the "load" command in GDB and have the code loaded into
    FLASH over the BLE connection.
    I was able to "load" a program into FLASH and then successfully run
    "compare-sections" to verify that the write was successful.
    [main.c]
2022-05-06 Fix FORWARD macro in gcc_startup_nrf52.S
    The exception number parameter to the FORWARD macro needed to be placed
    in paranthesis. Before external interrupts would use incorrect math to
    calculate the interrupt vector offset.
2022-05-06 High priority crashes stored in FLASH for later debugging
    68kB of FLASH are reserved for the storage of this dump:
    * 64kB to store the contents of SRAM at the time of crash.
    * 4kB to store a copy of mriCortexMState, including the
    state of the CPU registers.
    Once the crash has been stored in FLASH, the microcontroller is
    reset. I will later write code to detect the dump in FLASH after the
    reset and provide it to GDB for debugging instead of the actual CPU.
    [main.c]
2022-05-06 Add high priority crash to sample application
    Pressing button 3 causes an interrupt to fire at priority level 2 with
    an invalid read to cause a high priority fault for testing of the new
    dump code.
    [main.c, sdk_config.h]
2022-05-07 Add support for debugging crash dumps
    When a high priority interrupt generates a fault, there is code which
    dumps the CPU context and RAM contents to a reserved location in FLASH.
    This commit adds code which detects that such a crash dump after a
    reset and enters a special mode where MRI is used to debug this dump
    rather than the live CPU. It is actually hard for the user to even tell
    that anything different from a normal crash has occurred.
    To clear the crash dump, the user just needs to issue a "monitor reset"
    command in GDB.
    [main.c]
2022-05-12 Dump on debug events from high priority ISRs
    Can now trap debug events such as breakpoints being hit in high
    priority ISRs, even the BLE stack. This trap can then be used to
    generate a crash dump. While you can't single step or continue
    execution after hitting such a debug event, it still lets you do
    things like settings breakpoints or watchpoints that might get hit in
    high priority ISRs and see the state at the time of those debug events.
    [main.c]
2022-05-13 Add semihost support
    * Updated mriblue_boot to wrap mriPlatform_TypeOfCurrentInstruction()
    and mriSemihost_HandleNewlibSemihostRequest(). The original versions
    in MRI use a single "bkpt 0xff" instruction as a signal to thunk the
    call over to GDB. It used the program counter value of where the bkpt
    instruction was located to determine which syscall was needed. This
    doesn't work with the bootloader because it doesn't have access to
    the symbols of the robot code to know where the thunks are located.
    The wrapped versions of these functions use a different literal with
    the bkpt instruction for each syscall to determine which syscall is
    being made.
    * The robot code now contains c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
    [main.c]
2022-05-14 Writes to stdout no longer waits on GDB
    They just queue up a GDB 'O' (output) packet and then continue
    execution of the debuggee. While sending an 'O' packet would normally
    require waiting for GDB to ack it, I have modified the code to just
    pretend that GDB has acked the packet and then eat the ack (or nak)
    when GDB actually sends it. This means that calls from the robot code
    to printf() no longer block waiting for GDB to receive the data which
    can take awhile over the wireless BLE connection.
    [main.c]
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2022-05-14 Add "monitor resetbreak" command support
    This command allows the developer to enable or disable breaking into
    the debuggee's Reset_Handler on bootup. This is enabled by default and
    allows the developer to set breakpoints before the code even gets to
    the program's main(). You would disable it though if you want your
    code to just start and run and only halt if it crashes or you manually
    attach the debugger.
    [main.c]
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2022-05-22 Auto "monitor reset" after "load"
    No longer need to issue "monitor reset" after every "load" command. It
    no happens automatically in mriblue_boot.
    [main.c]
2022-05-23 Decrease BLE connection interval from 15ms to 7.5ms
    This is the smallest connection interval allowed and normally macOS
    will comply with it but I know that iOS will just drop the connection
    after a minute or so when it can't agree on the interval as it wants
    15ms as the shortest allowed.
    macOS is sending a maximum of 8 packets during a connection interval so
    decreasing it to 7.5ms results in less unused time in the connection
    interval. However, I am not always seeing macOS using this shorter
    connection interval for some reason.
    [main.c]
2022-06-05 Updates to the nrfSDK's QDEC driver
    It didn't handle the following cases:
    * Not using the LED pin as in my case since I am using hall effect
    based encoders.
    * Not handling scenarios where user doesn't want to get report
    interrupts from the QDEC peripheral for every so many samples. I
    don't want interrupts from it at all. I will pull the counter fast
    enough for the PID loop that it doesn't overflow.
2022-06-05 OLED_SH1106::clearScreen() resets cursor to upper left
    [OLED_SH1106.cpp]
2022-06-05 mriblue_boot no longer needs 32.768kHz crystal
    This frees up P0.0 and P0.1 for robot functionality in the future. This
    will increase current usage a bit I guess but I don't care since the
    robot's motors are so much more of a current hog that the nRF52 is
    noise.
    [main.c]
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2022-06-06 Incorrectly treating traps as semihosting requests
    The bkpt instruction range considered to be semihosting requests for
    mriblue were incorrectly checked (|| instead of &&) which lead to
    treating traps for things like watchpoints as a semihost request with
    random results. I had a watchpoint that would hit, get treated as a
    mriSetDebuggerHooks() request, corrupt the hook function pointers, and
    that resulted in the device resetting.
    I also fixed a memset() call to erase all of the items in the
    g_whitelistPeers array.
    [main.c]
2022-06-20 Update schematic to use correct pin for LMOTOR_PWM1
    [shield.kicad_sch]
2022-06-20 QuadratureDecoderSoftware::pinChanged() doesn't need to use atomic op
    The m_count member is only modified by the code in this method which is
    only run from the same ISR. This means it doesn't need to use an atomic
    add operation to modify its value.
    [QuadratureDecoderSoftware.cpp]
2022-06-20 mriblue_boot shouldn't configure P0.21 as reset
    The application being debugged should take care of setting the
    necessary bit in the UICR if they want to use the pin as the reset
    source. The current RugRover shield PCB uses P0.21 as a GPIO pin so
    it doesn't want it configured for reset.
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2022-06-27 Upgrade to latest MRI version
    MRI now automatically unescapes binary data so it no longer needs to be
    done in the writeToFlash() as it has already been done by MRI by the
    time it gets the data to be written to FLASH.
    [main.c]
2022-06-27 Couldn't CTRL+C when printf() spamming GDB
    nordicUartServiceHandler() would fail to break into MRI if MRI was
    already running to send out the next 'O'utput packet. I modified the
    mriblue_boot code to explicitly handle this situation.
    [main.c]
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2022-07-07 Refactor semihost usage of errno
    Now have to call mriNewlib_SemihostGetErrNo() to retrieve the errno
    associated with a failed semihost request. I have updated the
    newlib_retarget.c stubs to call this function when an error has been
    detected to then update the Standard C Library's errno value.
    I had to update the nrf52.ld for other changes in this version of the
    MRI library which increased the demand on RAM by one more 32-bit word.
    [main.c]
2022-07-07 Handle crash dump reset when at breakpoint
    When a crash dump is generated for a breakpoint that is encountered
    when running high priority code, things need to be done a bit
    differently to keep GDB happy:
    * GDB knows that the PC register is pointing at an instruction that it
    has set a breakpoint at so it will treat it as such even though MRI
    reports it as a crashing debug event.
    * When the user types "monitor reset" and then "continue", GDB will
    first ask MRI to single step over the breakoint before issuing
    the continue.
    * When mriblue_boot was debugging a crash dump, it would do nothing
    for single step instructions. This confuses GDB in this scenario
    since it expects the PC to ad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
    [main.c]
2022-07-07 Clean out crash dump on "load" command
    The crash dump would be associated with the previous version of the
    code so mark it as invalid and prepare for a CPU reset to run the new
    code.
    [main.c]
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2022-07-18 Add SYSLIBS for libs like -lc -lnosys -lm
    The "-u _printf_float" flag was causing me issues since it pulled in
    syscalls from libnosys.a instead of my newlib_retarget.c This happened
    because Makefile.common included the -l -lnosys -lm libs on the linker
    command line before the object files. I now use a SYSLIBS variable to
    include these libraries after the object files if I want instead of
    placing them in the LD_FLAGS variable.
    I also removed the duplicate newlib_stubs.h from the
    mriblue_boot/shared folder and just use the one in the MRI folder
    instead. The one in this folder was old and stale.
    [main.c]
2022-07-18 Enable PID code to run closed loop
    The main test is now ramping up and down through a range of desired
    rotational velocities rather than motor power settings. The PID code
    takes care of ramping the motor power up and down to maintain the
    desired velocities.
    The PID parameters were calculated based on the results generated from
    a run of the testPidCalibrateRoutine() while the bot was down on the
    floor.
    I changed back from RPM to encoder ticks per sample for measuring
    velocity since a +/- 1 tick difference per tick can generate much
    larger changes in RPM values which would cause the PID loop to
    oscillate too much as it encounterd these little variances in tick
    per sample count.
    [DifferentialDrive.cpp, main.cpp]
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2022-07-18 Update PID limits with latest motor driver limits
    The TB9051FTG Motor Driver doesn't allow immediate switching from one
    direction to another. This update asks the motor driver for its current
    limits and passes them along to the PID loop so that it knows if the
    motor power will be clamped and take it into account in its integral
    windup correction code.
    [DifferentialDrive.cpp, DualTB9051FTGDrivers.cpp]
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2022-07-19 Added capacityUsed_mAh to DriveStats
    This is an attempt to estimate how much battery capacity has been
    consumed by the motors since reset. Can be used later to estimate
    when the batteries should be recharged since the motors will probably
    be the largest consumer of battery power.
    [DifferentialDrive.cpp, main.cpp]
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2022-08-06 Navigation improvements
    This commit is an attempt to make navigation a bit more robust but I
    still have more work to do yet to make it rock solid:
    * Added a reset method to the PID class and call it from the
    Navigate::reset() method.
    * Add Navigate constructor parameters for the distance and angle
    thresholds used to determine when a waypoint has been reached.
    * Navigate::setWaypointVelocity() is now
    Navigate::setWaypointVelocities() so that separate values can be used
    for the maximum steering and driving rates used when navigating
    between waypoints.
    * Navigate::update() used to only stop traveling towards a waypoint
    when the distance threshold was met. This meant that it could tr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
    [Navigate.cpp, main.cpp]
2022-08-09 Add logging capability to Navigate class
    * Added a setLogBuffer() method which allows the user of the Navigate
    class to pass in an array of memory to be used as a circular buffer
    into which encoder ticks and motor power can be logged. This allows
    the user to determine the size of the buffer to be used and where it
    is to be located (stack, heap, etc).
    * Added a dumpLog() method which uses the data in the circular log to
    create a .CSV file on the PC with the caller specified name. It dumps
    the entries in reverse order as that makes it easier to roll
    backwards things like the time, absolute encoder tick counts, and
    absolute robot position/heading for each row.
    * I added a Naviga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
    [Navigate.cpp, main.cpp]
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2022-08-11 Track position during slow down
    Before I was braking the two wheels but I didn't allow the Navigate
    module to updates its estimate of the robot's position and heading in
    the real world.
    [Navigate.cpp, main.cpp]
2022-08-11 Reset heading PID limits once waypoint is reached
    [Navigate.cpp]
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2022-08-11 Expose PID frequency from DifferentialDrive
    * Added getPidFrequency() to DifferentialDrive class so that this
    frequency can be accessed from other modules.
    * Navigate class no longer needs the PID frequency passed into its
    constructor since it can now pull it from the m_pDrive member using
    the above method.
    * I added _Hz suffix to frequency parameters in DifferentialDrive
    class to make the units clearer to users.
    [DifferentialDrive.cpp, Navigate.cpp, main.cpp]
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2022-08-13 Forgot photos for prev commit
    I also fixed some spelling mistakes in software/main.cpp that I noticed
    once I started using the spell checker extension in my code editor.
    [main.cpp]
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2022-09-08 TWIM and build patches for nrfSDK
    * Don't set STOP task again if NAK is received on last byte in a write
    since that will cause another STOP to be issued just before the next
    START should be generated. This patch is for the blocking version of
    the write call.
    * Fix build error in TWIM driver when compiled as C++ instead of C.
    * Updated nrf5x_common.ld to push the .data section initialization
    data to FLASH using a different syntax. This new syntax allows the
    linker to generate errors when the .data section overflows FLASH.
    Previously mriblue_boot images could actually use more FLASH than they
    were supposed to and no linker error would be generated. This meant
    that crash dumps w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
2022-09-09 Updates to IMU source code header comments
    The Kalman filter/IMU source code files that I pulled over from my
    Ferdinand20 project were missing descriptive comments at the top
    indicating what each module does. I noticed this when updating the
    README with descriptions about the new modules that I recently added to
    this project.
    [FXAS21002C.cpp, FXOS8700CQ.cpp, SensorBase.cpp]
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2022-09-09 Fix potential race condition in I2CAsync
    Now use a mutex to make sure that there is 1 and only 1 TWIM transfer
    in progress when a new read/write operation is queued up. If there is
    already a transfer in progress then the ISR will take care of issuing
    the next one. If not then one producer (and only 1 producer) will be
    selected to pull the oldest item from the circular buffer and submit it
    to the TWIM peripheral and then the ISR can handle any more that are in
    the queue.
    [I2CAsync.cpp]
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2022-09-14 Improve navigation back to origin
    This goal of this commit was to get the robot navigating back to what
    it thinks is the origin (0, 0) as closely as possible. The robot might
    not get back to the origin in the real world but that is a different
    problem that I will tackle later by tweaking wheel diameters and
    wheelbase.
    * I fixed a bug in the navigation module distance PID constants. I had
    set the Td constant with what should have been the Ti constant when
    the Td constant was supposed to be 0. Making this fix stopped the
    robot taking the wide turns around the corners like it used to
    before.
    * I added a braking stage between the driving to the next waypoint and
    then turning to face th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
    [Navigate.cpp, main.cpp]
2022-09-14 Add compass heading to navigation test
    Just logs the IMU calculated orientation/heading to the OLED and PC over
    the BLE data connection.
    It waits 5 seconds at the beginning of the test run for the Kalman
    filter to stabilize.
    [main.cpp]
2022-09-14 Navigate module improvements
    Improvements include:
    * Brake before and after ROTATE_TO_HEADING. This means that
    testDriveWaypoints() in main.cpp no longer needs to wait for the
    robot to stop moving before it ends the test run. Once the
    navigate module says the last waypoint is reached then the caller
    knows that the robot is no longer in motion.
    * Now apply 1 update iteration of braking between the ROTATE_TO_NEXT
    and DRIVE_TO_NEXT stages. This gets both motors in a state that they
    can turn in either direction (can't immediately switch the motor
    direction with the current motor drivers) and clears out the integral
    component that may be limiting the output to maintain with curren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
    [Navigate.cpp, main.cpp]
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2022-09-15 Fix TWIM ERROR & STOPPED race condition
    Sometimes the I2C master ends up sending 2 stops because the driver gets
    confused when the last byte is NAKed by the slave. Sometimes this
    generates an ERROR event before the STOPPED event and other times it
    happens in the reverse order. I already added a fix for this in the
    blocking code path of the TWIM driver in the Nordic SDK. This commit
    adds a fix for the non-blocking interrupt driven version too.
    I have improved the previously made linker script fix for the .data
    section to make sure that the __etext symbol is given the correct
    value, taking into account that the new AT usage may change alignment.
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2022-09-19 Navigate w/ IMU and start of new Kalman filter
    I updated the Navigate module so that it can now use the compass heading
    determined from the IMU based Kalman filter or just use the wheel
    odometry. The test results weren't that good. It seems to be mostly
    related to magnetic interference in the house. Worked better outside.
    Based on the poor 3D orientation Kalman filter, I have started thinking
    about a new Kalman filter which just combines the yaw rate gyro output
    with the wheel odometry calculated heading to see if that can generate
    some improvements. This commit includes my initial work in this area
    which includes the system model and code to determine what kind of
    errors it generates.
    I a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
    [Navigate.cpp, main.cpp]
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
